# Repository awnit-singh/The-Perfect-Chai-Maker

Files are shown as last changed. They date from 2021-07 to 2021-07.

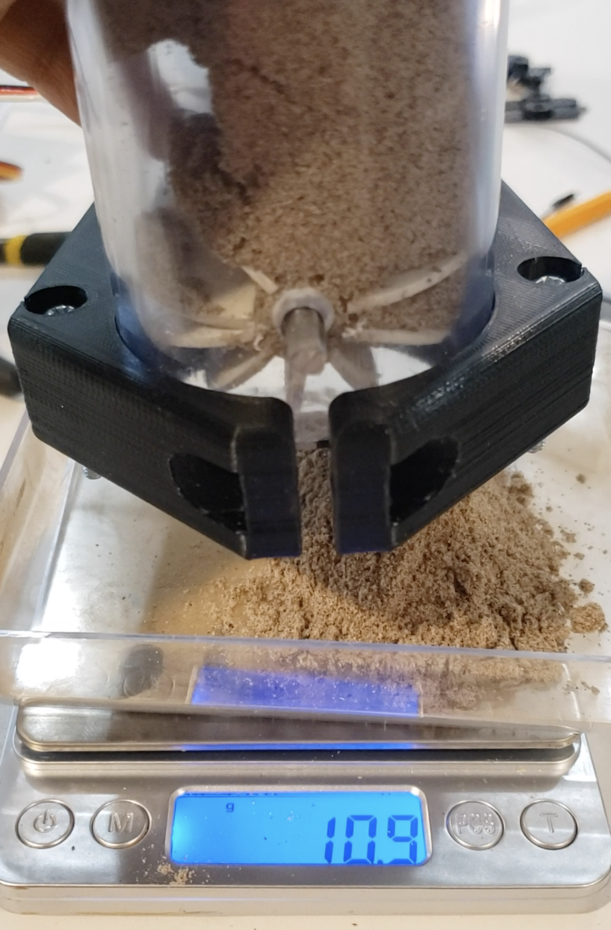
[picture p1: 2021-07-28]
Pictures/Cardamom-Measurement.png

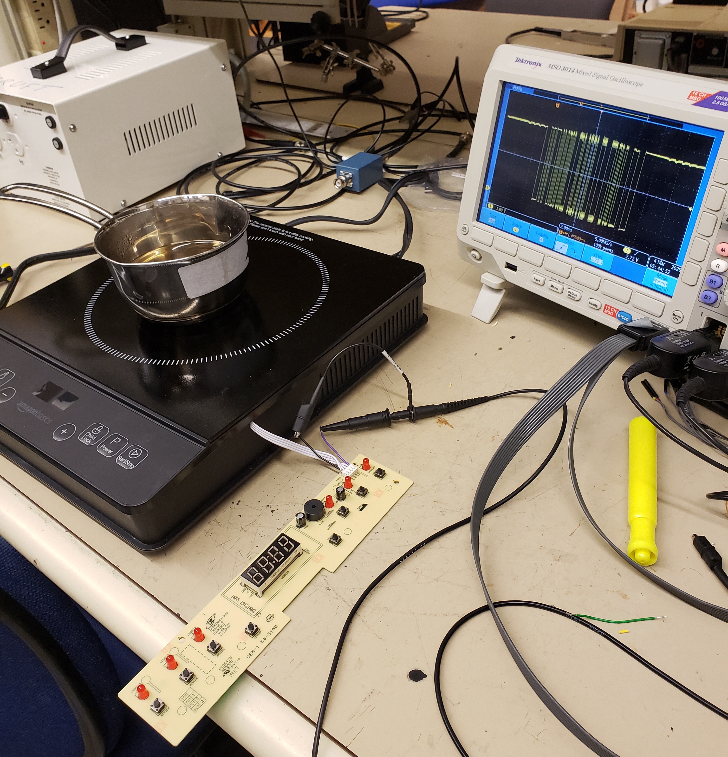
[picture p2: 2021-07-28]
Pictures/Milk-Heater-Setup.jpg

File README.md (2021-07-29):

# The-Perfect-Chai-Maker
Senior Engineering Design Project for Electrical Engineering (Honors).
https://dash.harvard.edu/handle/1/37366965

This senior thesis project presents The Perfect Chai Maker, a machine capable of making masala chai, a South Asian tea beverage, automatically. Chai is a method of making tea rather an a flavour itself. With an increasing demand for chai in the American and European market, prod- ucts have failed to replicate the traditional recipe or to improve on the inconvenience currently associated with making chai – such as time taken for preparation of the ingredients and super- vising the recipe when on the heat. This machine follows strict tolerances based on a modified version of a chai recipe to replicate a traditional cup of chai. The milk is inserted to the machine by the user though it self dispenses ingredients and hot water, taking a total of less than 5 min- utes to operate. Most of the specifications were met for the machine.
Please note that the concluding three weeks of this project were cut short due to com- plications related to the COVID-19 pandemic.

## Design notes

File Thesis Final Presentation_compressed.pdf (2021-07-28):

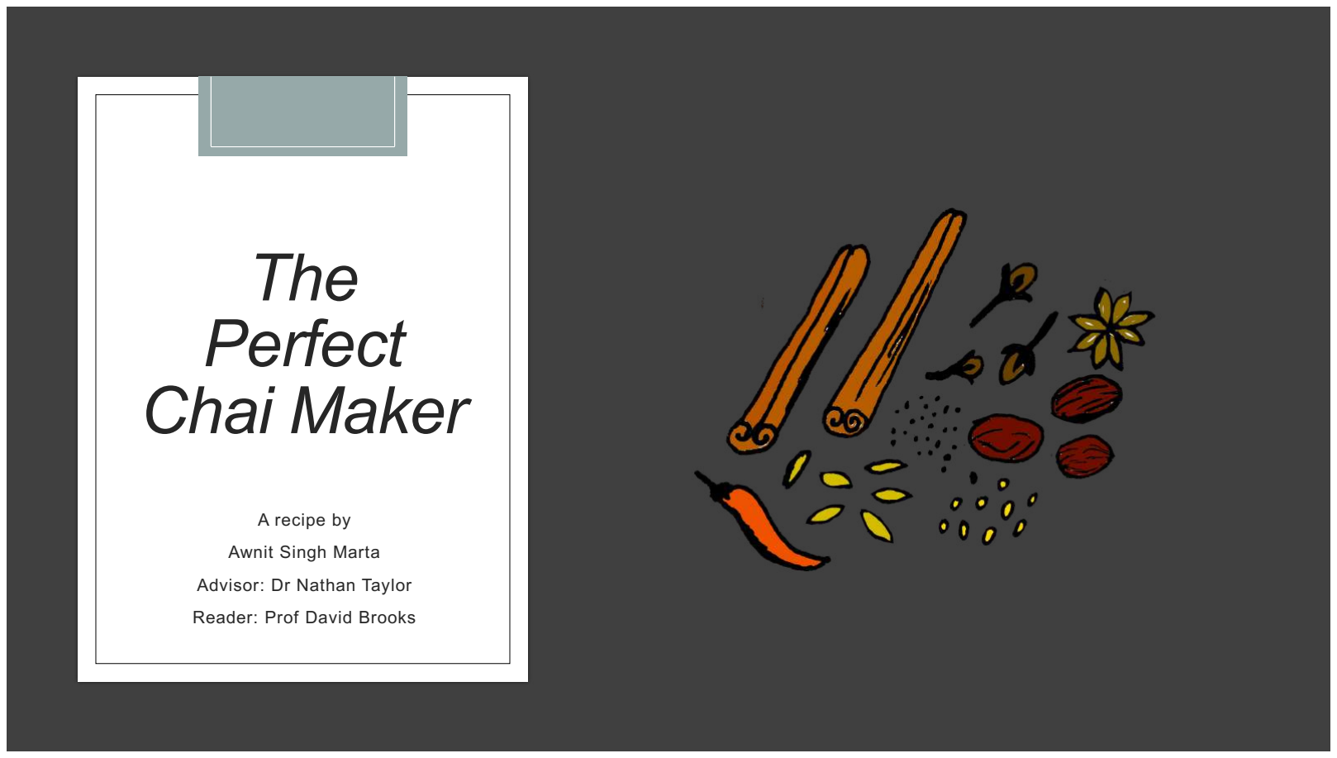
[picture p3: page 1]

# The Perfect Chai Maker

A recipe by
Awnit Singh Marta
Advisor: Dr Nathan Taylor
Reader: Prof David Brooks

# Problem

Institute for Scientific Information on Coffee, “The good things in life: coffee in the workplace,” Worcestershire, 2017.

Chai: a flavour NOT a process No dedicated chai machine in market

2 billion tea drinkers ↑+ in American market (Starbucks, Peet’s, 7/11)

67% drink ‘hot beverages’ at workplace: taste, socialize, pause & rest

Define | Design | Build | Measure | 2

# Problem

Institute for Scientific Information on Coffee, “The good things in life: coffee in the workplace,” Worcestershire, 2017.

Chai: a flavour NOT a process No dedicated chai machine in market

2 billion tea drinkers ↑+ in American market (Starbucks, Peet’s, 7/11)

67% drink ‘hot beverages’ at workplace: taste, socialize, pause & rest

Making coffee at the workplace has become an integrated part of workflow, generally requiring just the TOUCH OF A BUTTON to make. However, making Chai, a South Asian tea, has required more TIME, HANDLING of multiple components, and SUPERVISION through the process.

Define | Design | Build | Measure | 3

# Background/Existing Work

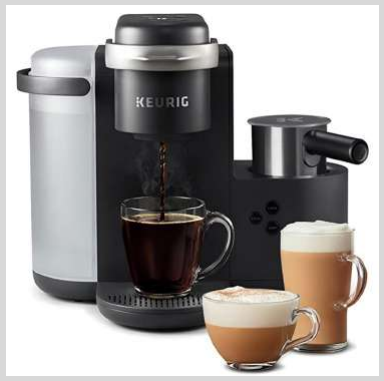
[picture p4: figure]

$199 | $220 | $250 | $450
Define | Design | Build | Measure | 4

Teas
- Insert everything
manually
- Strainer
- Induction
heater

Hot beverages
- Pod ingredients
- Reservoir for water
- Milk separately inserted
- Induction heater +
heating element

Chai
- Pod ingredients integrated
- Reservoir for water
- Milk integrated with chai
- Induction heater +
heating element

Espresso
- Pod ingredients
- Fully automated to glass
- Reservoir for water, milk
- Milk steamer + heating
element

PRODUCE | TRADITIONAL RECIPE

Chai in under 5 minutes

# Goal

Making coffee at the workplace has become an integrated part of workflow, generally requiring just the touch of a button to make. However, making Chai, a South Asian tea, has required more time, handling of multiple components, and supervision through the process.

Heat water
to 93°C
(3 min)

Insert: tea,
spices,
sugar

Simmer
(2 min)

Add milk,
bring to
boil
(3 min)

Simmer
(2 min)

Strain and
enjoy Chai!
Integrated ingredients

Minimal user involvement

S. Fountaine, “authentic masala chai recipe!,” feasting at home, 2 January 2019. [Online]. Available: https://www.feastingathome.com/authentic-masala-chai-recipe/. [Accessed 30 September 2019].
J. Pallian, “Authentic Homemade Indian Chai,” foodess, 29 November 2016. [Online]. Available: https://foodess.com/authentic-indian-chai-tea-recipe/. [Accessed 30 September 2019].
Define | Design | Build | Measure | 5

# Technical Specifications

Define | Design | Build | Measure | 6
Water temperature Milk temperature | 96 °C 85 °C | + 1 °C, − 4 °C + 5 °C, − 0 °C
Water pumped | 180 mL | ± 15 mL
Tea Cardamom and fennel seeds Sugar | 2.0 1.0 8.0 | ± 0.4 g ± 0.2 g ± 2.0 g
Time taken | < 5 mins
Size | 50 cm x 50 cm x 50 cm

PRODUCE | TRADITIONAL RECIPE

Chai in under 5 minutes

# Goal

Making coffee at the workplace has become an integrated part of workflow, generally requiring just the touch of a button to make. However, making Chai, a South Asian tea, has required more time, handling of multiple components, and supervision through the process.

Heat water
to 93°C
(3 min)

Insert: tea,
spices,
sugar

Simmer
(2 min)

Add milk,
bring to
boil
(3 min)

Simmer
(2 min)

Strain and
enjoy Chai!
Integrated ingredients

Minimal user involvement

S. Fountaine, “authentic masala chai recipe!,” feasting at home, 2 January 2019. [Online]. Available: https://www.feastingathome.com/authentic-masala-chai-recipe/. [Accessed 30 September 2019].
J. Pallian, “Authentic Homemade Indian Chai,” foodess, 29 November 2016. [Online]. Available: https://foodess.com/authentic-indian-chai-tea-recipe/. [Accessed 30 September 2019].
Define | Design | Build | Measure | 7

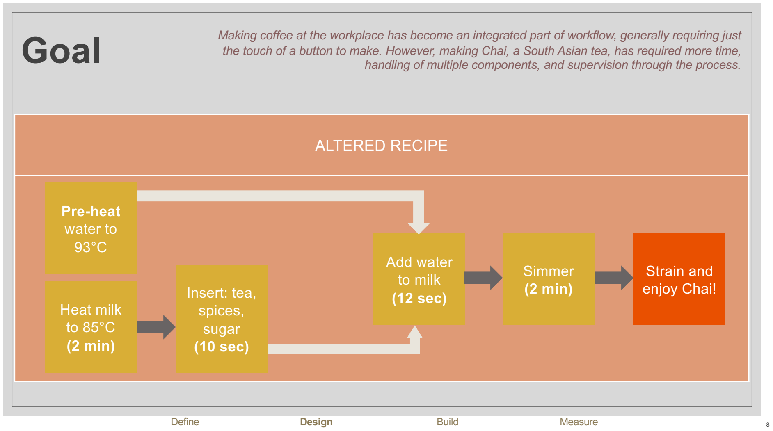
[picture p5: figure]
ALTERED RECIPE; Goal; Pre-heat water to 93°C; Heat milk to 85°C (2 min); Simmer (2 min); Strain and enjoy Chai!; Add water to milk (12 sec) Insert: tea, spices, sugar (10 sec); Define; Design; Build; Measure

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

# System Overview

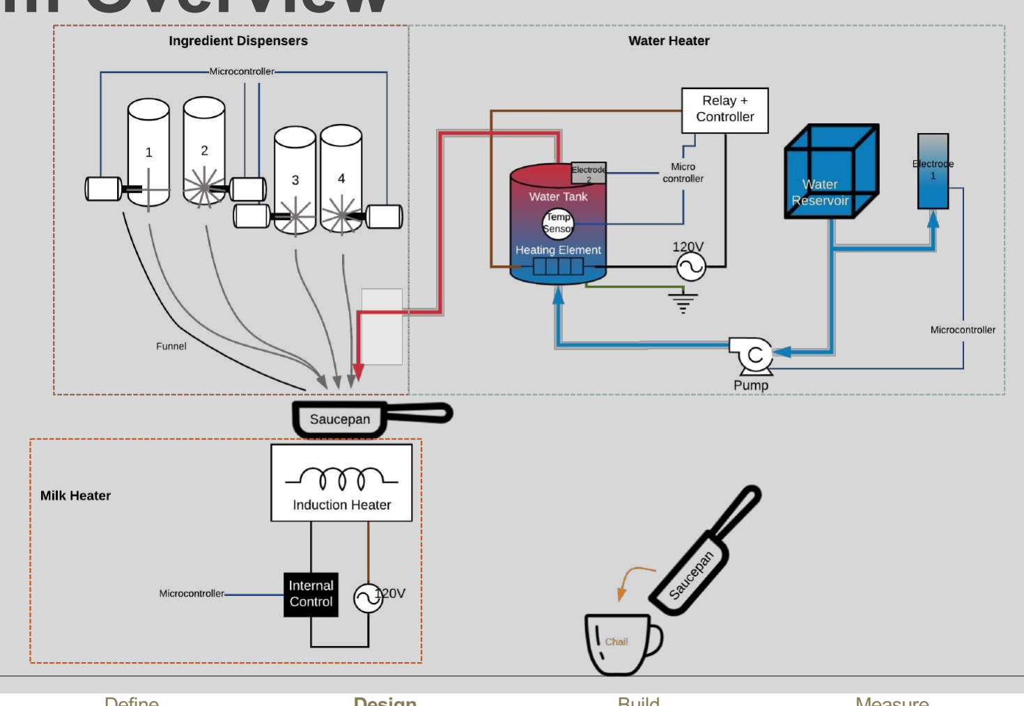
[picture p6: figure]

Define | Design | Build | Measure | 9

# System Overview

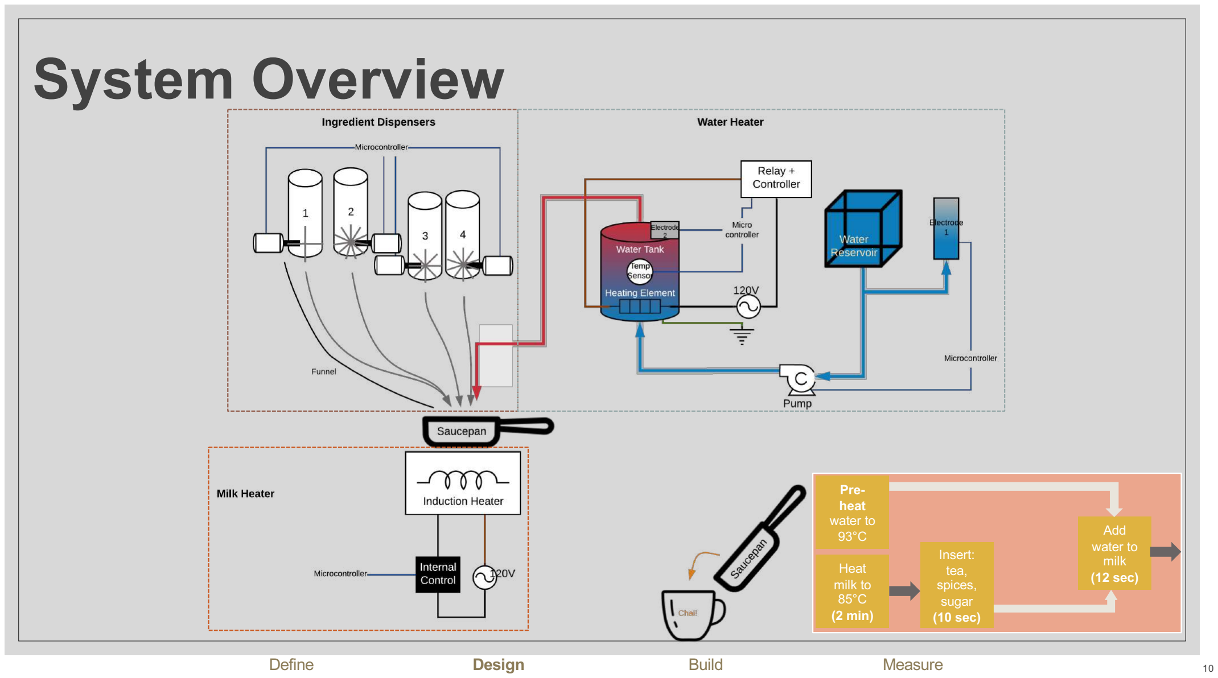
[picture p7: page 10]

Define | Design | Build | Measure | 10

Pre-heat
water to
93°C

Heat
milk to
85°C
(2 min)

Add
water to
milk
(12 sec)

Insert:
tea,
spices,
sugar
(10 sec)

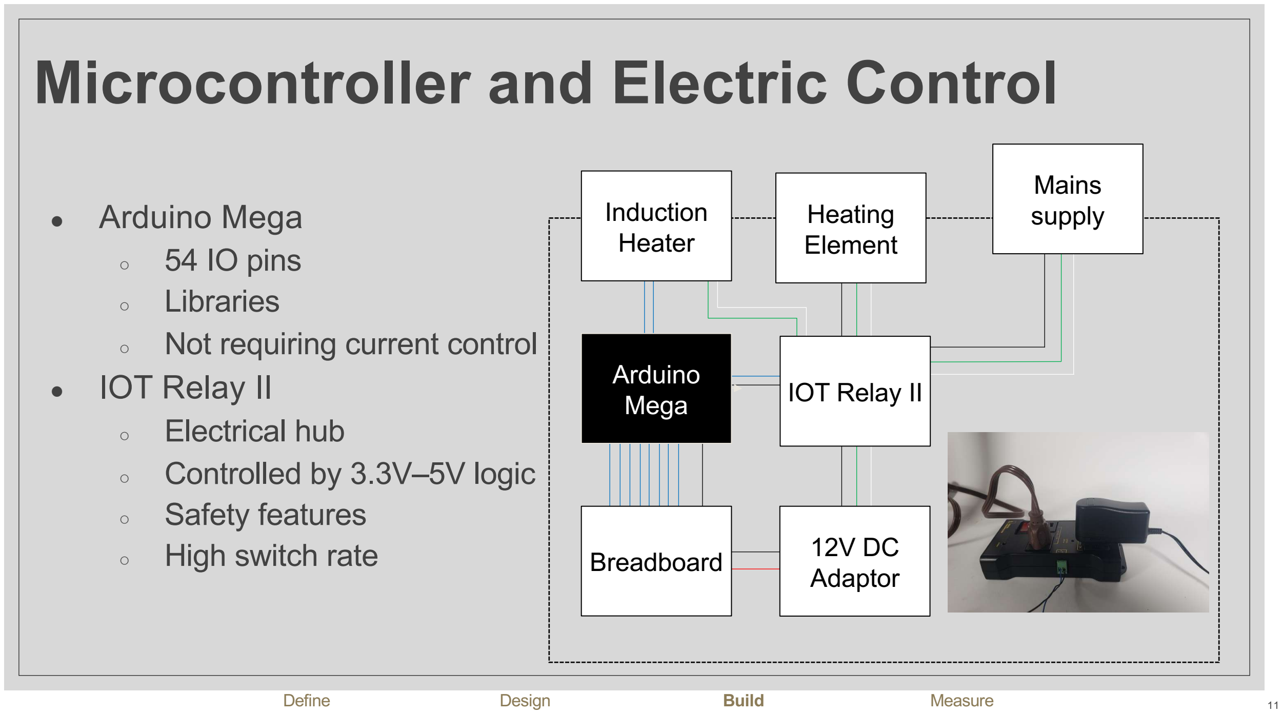
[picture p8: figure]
Microcontroller and Electric Control; ● Arduino Mega ○ 54 IO pins ○ Libraries ○ Not requiring current control ● IOT Relay II ○ Electrical hub ○ Controlled by 3.3V–5V logic ○ Safety features ○ High switch rate; Arduino Mega; Breadboard; Induction Heater; Mains supply; IOT Relay II; Heating Element; Define; Design; Build; Measure; 12V DC Adaptor

# Water Heater and Controller

12

- Water tank
- Sealed container – repurposed Keurig
- Internally secured temperature sensor

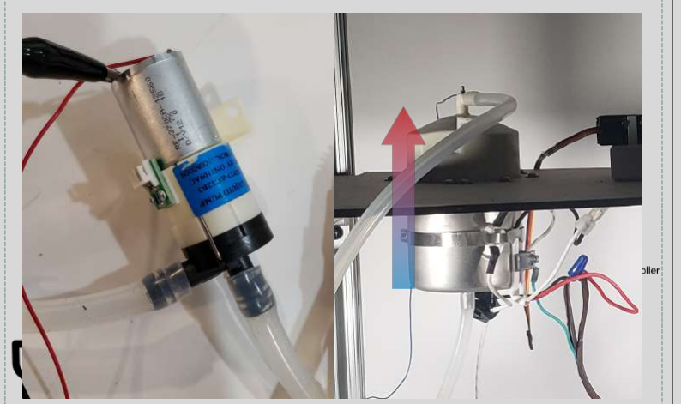
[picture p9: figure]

- Cold water enters through bottom (from reservoir), hot water leaves from top
- Keurig Water Pump
- Water flow rate within specified time
Define | Design | Build | Measure

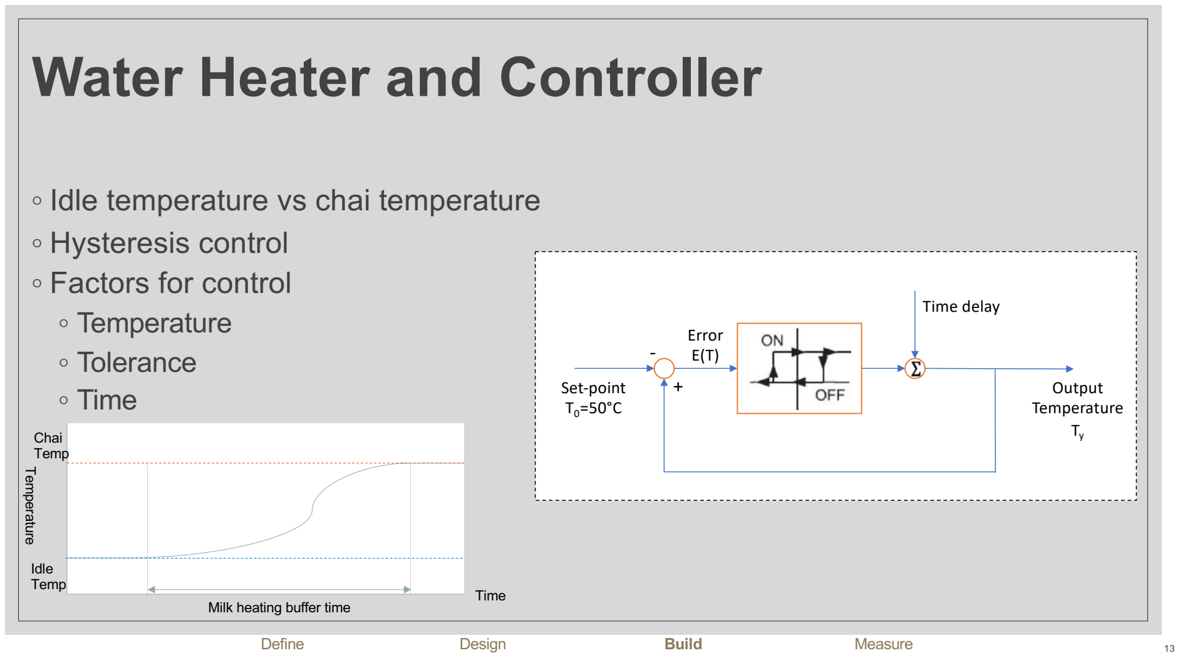
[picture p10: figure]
Water Heater and Controller; ◦ Idle temperature vs chai temperature ◦ Hysteresis control ◦ Factors for control ◦ Temperature ◦ Tolerance ◦ Time; Temperature Sensor; Water reservoir; Set-point T0=50°C; Error E(T); Time delay; Output Temperature Ty; Define; Design; Build; Measure; Idle Temp; Chai Temp Temperature; Time; Milk heating buffer time

# Ingredient Dispenser

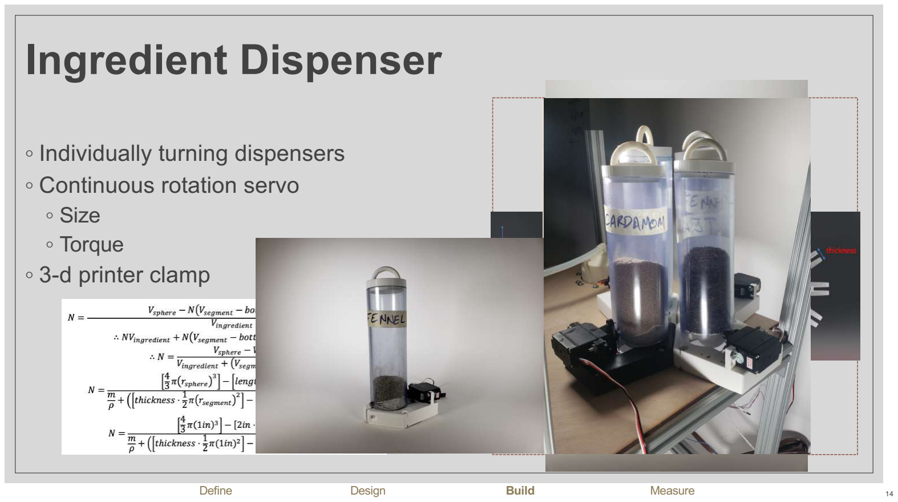
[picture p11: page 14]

14

- Individually turning dispensers
- Continuous rotation servo
- Size
- Torque
- 3-d printer clamp
Define | Design | Build | Measure

15

# Milk Heater

- Heating element vs induction heater
- Commercial conduction heater
- Tap into controls
- Safety
- Size

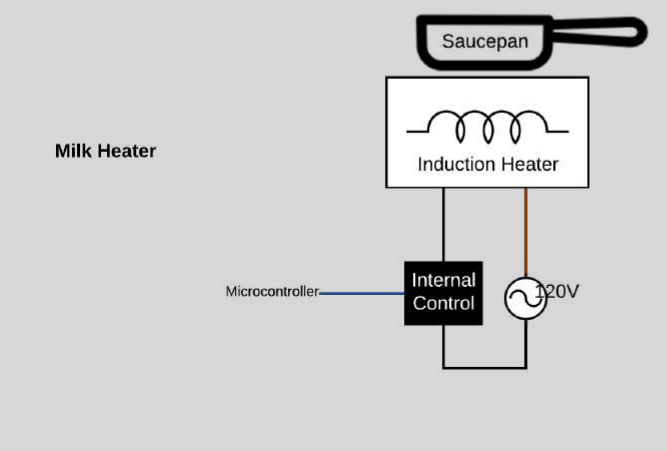
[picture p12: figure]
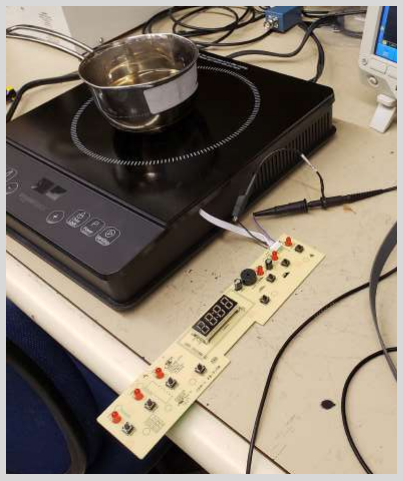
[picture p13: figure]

Define | Design | Build | Measure

# Milk Heater

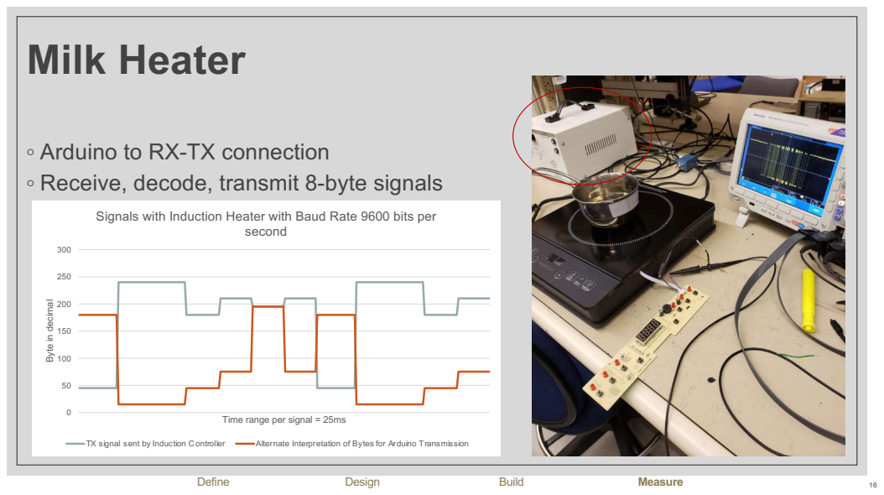
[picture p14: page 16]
second; TX signal sent by Induction Controller; Alternate Interpretation of Bytes for Arduino Transmission; Define; Design; Build; Measure

◦ Arduino to RX-TX connection
◦ Receive, decode, transmit 8-byte signals

Signals with Induction Heater with Baud Rate 9600 bits per

Byte in decimal

Time range per signal = 25ms

# Water Heater and Controller

17

- Time based
- Flowrate, rroom = 11.8 mLs⁻¹
- Flowrate, rchai = 15.0 mLs⁻¹
- Wider spread of volume but within tolerance

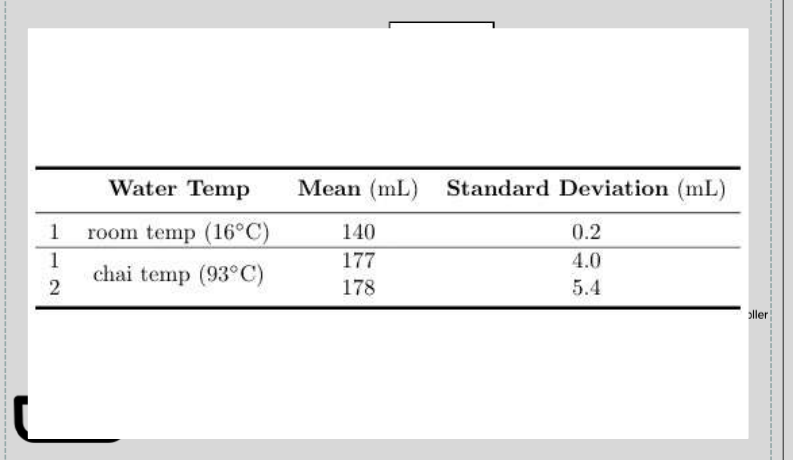
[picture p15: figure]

Define | Design | Build | Measure

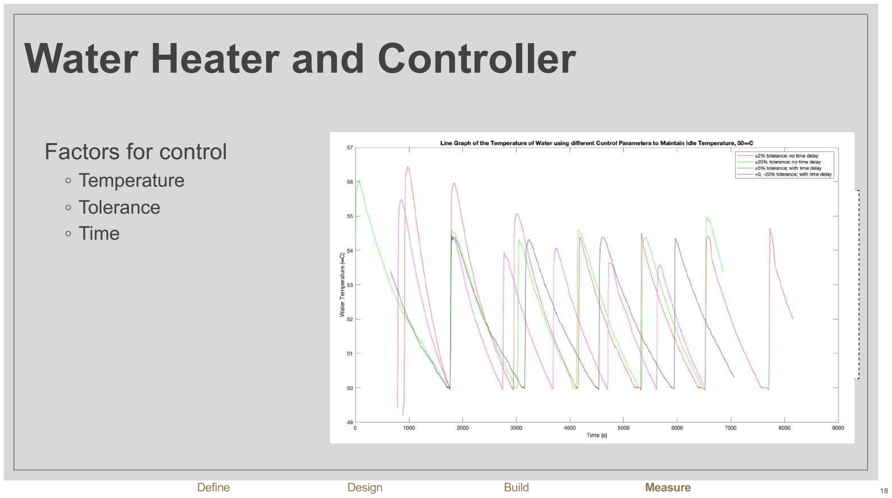
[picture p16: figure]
Water Heater and Controller; Factors for control ◦ Temperature ◦ Tolerance ◦ Time; Temperature Sensor; Water reservoir; Set-point T0=50°C; Error E(T); Time delay; Output Temperature Ty; Define; Design; Build; Measure

# Water Heater and Controller

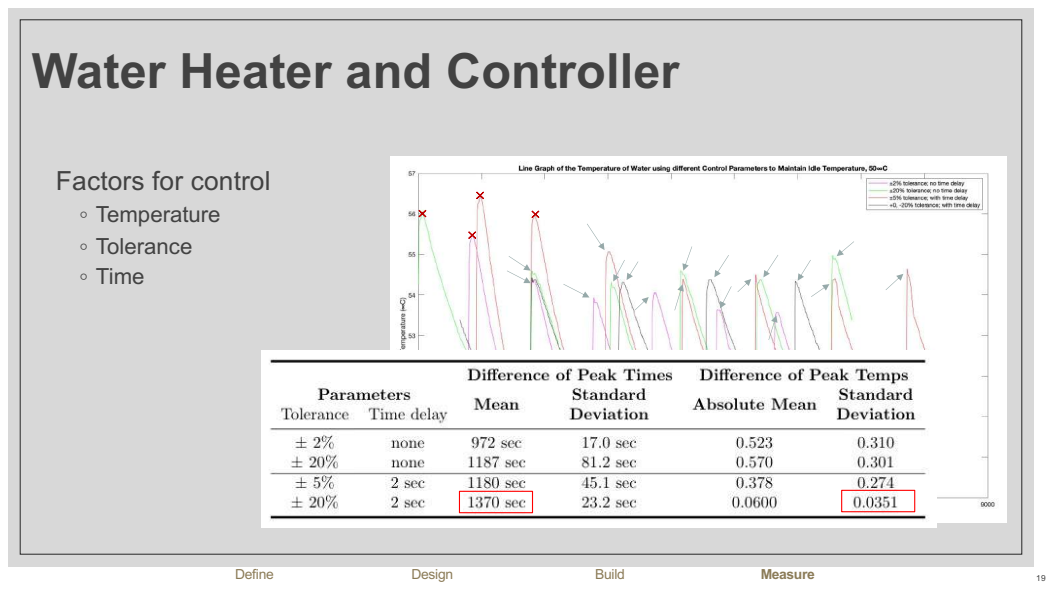
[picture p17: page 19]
Define; Design; Build; Measure

Factors for control
◦ Temperature
◦ Tolerance
◦ Time

# Ingredient Dispenser

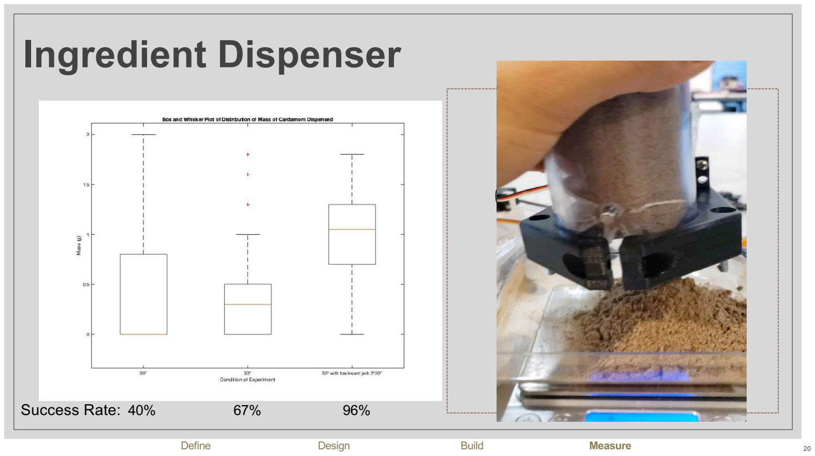
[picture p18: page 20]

20

Define | Design | Build | Measure
Success Rate: 40% | 67% | 96%

# Final Prototype

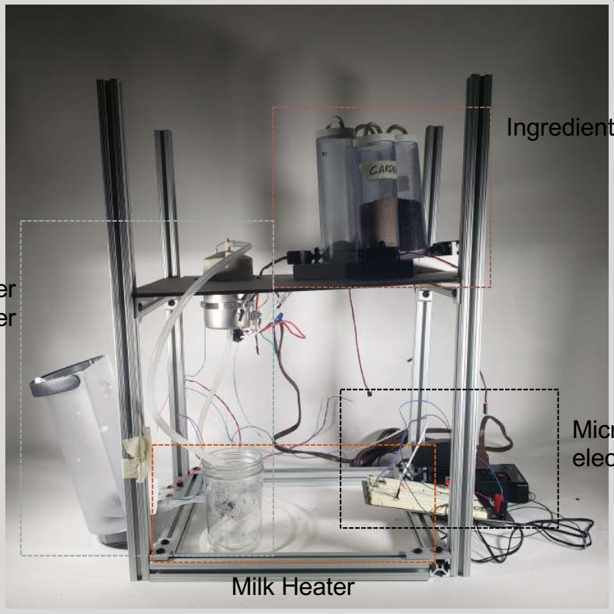
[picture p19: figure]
Milk Heater

Water
Heater

Microcontroller and
electric control

Ingredient Dispenser

21

Water temp Milk temp | 96 + 1°C, − 4°C 80 + 5°C, − 0°C | Yes Yes but not integrated
Water pumped | 180 ml ± 15 ml | Yes
Tea Cardamom and fennel seeds Sugar | 2.0 ± 0.4 g 1.0 ± 0.2 g 8.0 ± 2.0 g | Yes but tolerances not met
Time taken | < 5 mins | No
Size | 50 cm x 50 cm x 50 cm | Yes

# Conclusions

22

# Future Plans

23

Integration

Testing
Time entire process
Milk heater using immersed sensor Stable surface for ingredient dispensers Idle power usage for water heater

Tubing fitted with pressure valves PID water controller
Mixed spice dispenser

# did it make chai?

24

# thank you

25

## Nishant Nathan Evan Jim and Ben Salma ES Funhundred and the entire ES100 staff

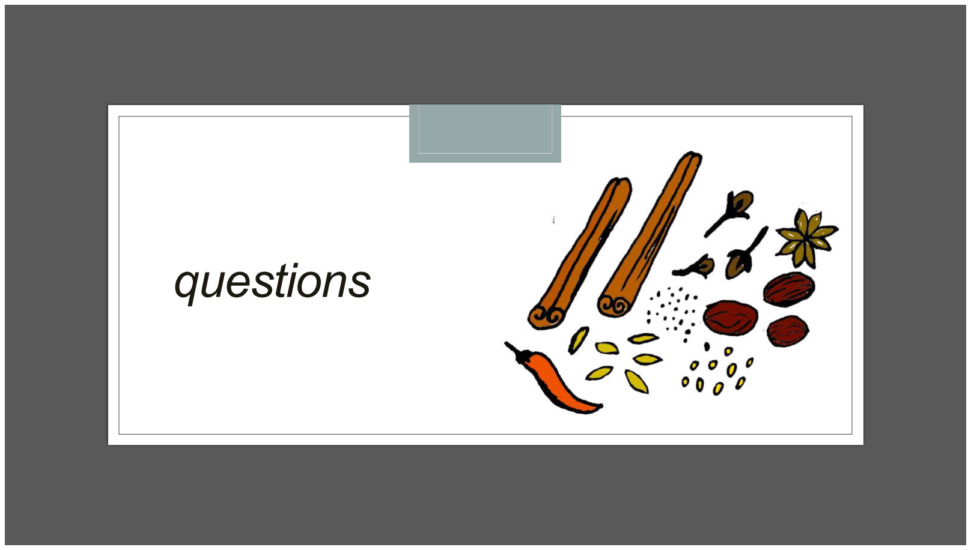
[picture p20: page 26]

# questions

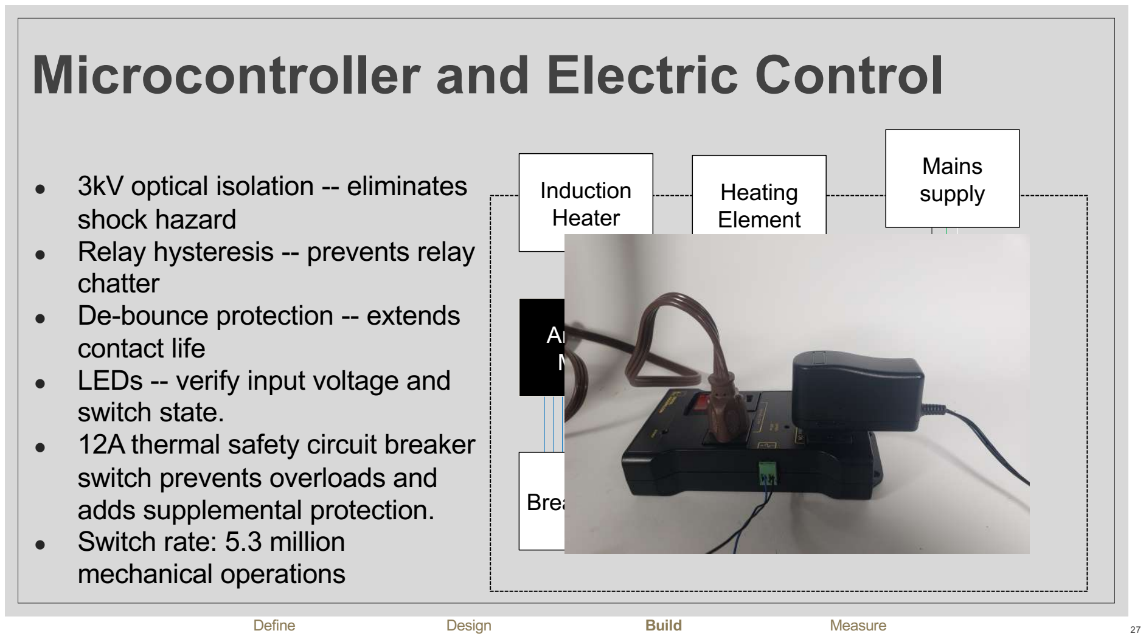
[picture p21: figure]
Microcontroller and Electric Control; ● 3kV optical isolation -- eliminates shock hazard ● Relay hysteresis -- prevents relay chatter ● De-bounce protection -- extends contact life ● LEDs -- verify input voltage and switch state. ● 12A thermal safety circuit breaker switch prevents overloads and adds supplemental protection. ● Switch rate: 5.3 million mechanical operations; Arduino Mega; Breadboard; Induction Heater; Mains supply; IOT Relay II; Heating Element; Define; Design; Build; Measure; 12V DC Adaptor

# Water Heater and Controller

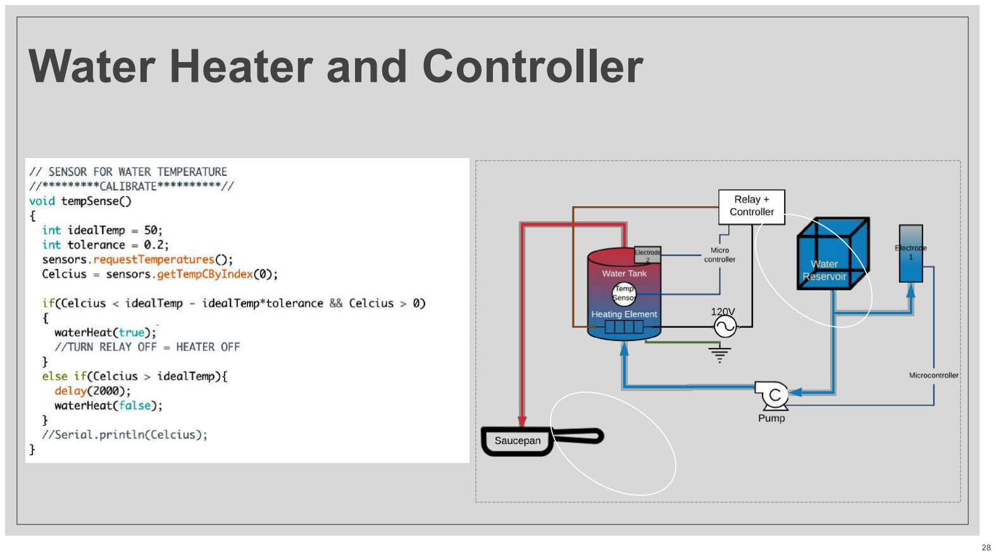
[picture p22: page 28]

28

- Verification of Presence of Water
- Electrodes in reservoir – active high
- Electrode on water tank – active low

# Water Heater and Controller

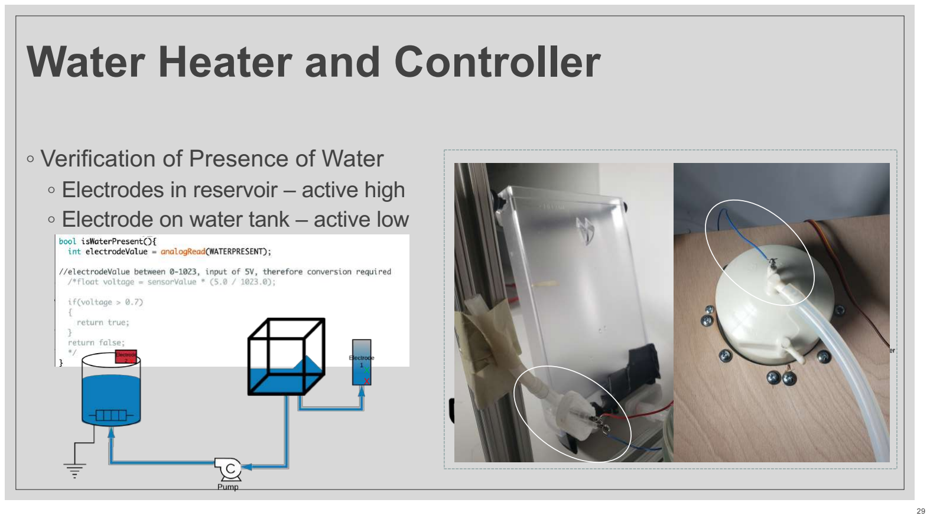
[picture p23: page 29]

29

- Verification of Presence of Water
- Electrodes in reservoir – active high
- Electrode on water tank – active low

X
X

X

Design Choices ◦ Milk inside machine? ◦ Refrigeration ◦ Clogging/cleaning of tubes ◦ Separate brewing chambers ◦ Spice choices ◦ No pods ◦ Cinnamon, ginger not used ◦ Not all required ◦ Wet vs dry ingredients ◦ Density of ingredients

30

# Water Heater and Controller

- Heating water to chai temperature
- Time = 200 sec

31

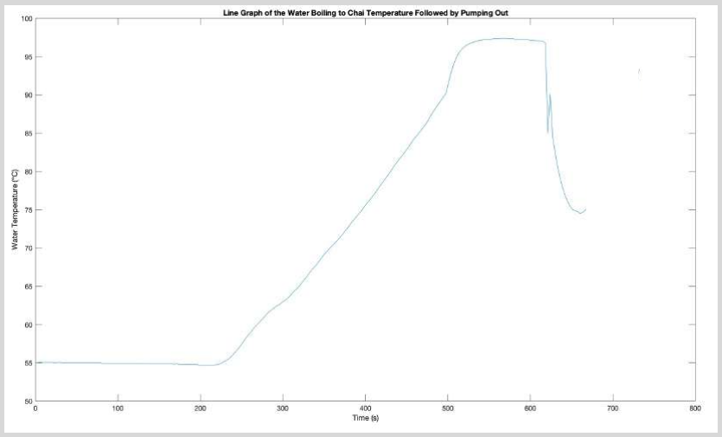
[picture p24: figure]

# Milk Heater

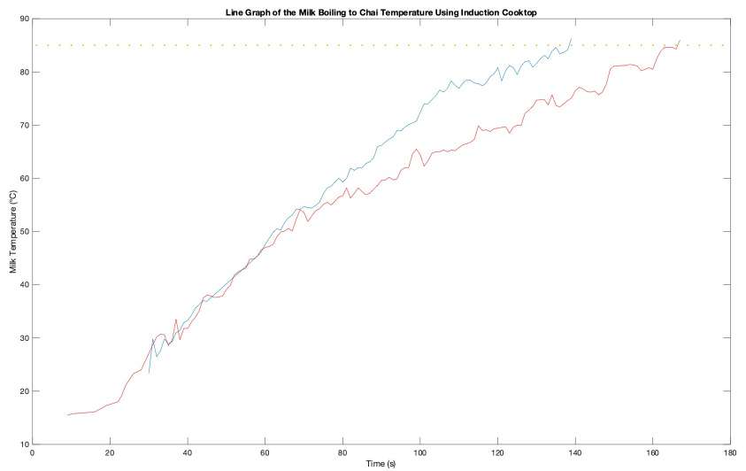
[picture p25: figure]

- Heating milk to chai temperature
- Time = 110 sec – 180 sec
- Conducted using IR sensor

32

# Ingredient Dispenser

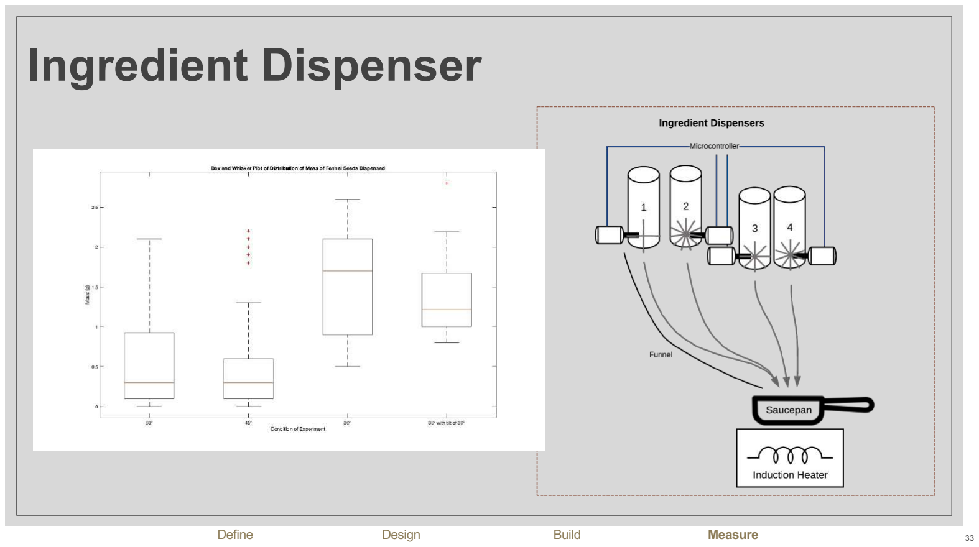
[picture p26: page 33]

33

Define | Design | Build | Measure

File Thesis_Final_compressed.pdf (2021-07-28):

# THE PERFECT CHAI MAKER

# AWNIT SINGH MARTA

Supervising Advisor: Dr Nathan Taylor Faculty Advisor: Professor David Brooks

A Senior Design Project submitted in partial fulfillment of the requirement for the degree of
Bachelor of Science in Electrical Engineering

John A. Paulson School of Engineering and Applied Sciences Harvard University

Cambridge, Massachusetts

April 10, 2020

## Contents

1 Introduction | 1
2 Problem Definition | 6
3 Design Approach | 10
4 Hardware Design | 12

i

5 Final Prototype and Conclusions | 43
6 Future Development | 45
7 Acknowledgements | 48
Appendices | 49
A Bill of Materials | 49
B Schematic | 50
C Arduino Code | 51
D Data Collection | 57

ii

D.1 Ingredient Tolerance Test | | 57
D.2 Calculating Ingredient Density | | 57
D.3 Dispensing Ingredients | | 58
D.4 Induction Heater Signals | | 61
E Data Sheets | 66

## List of Figures

1 | Study on drinking hot beverages | | 1
2 | CRAFTEA Machine | | 2
3 | Keurig K-Caf´e | | 3
4 | BrewChime Machine | | 4
5 | Nespresso Latisima Pro Machine | | 5
6 | Chai recipe | | 6
7 | Modified chai recipe | | 7
8 | Modified chai recipe flowchart | | 10
9 | System diagram | | 11
10 | Breadboard | | 12
11 | Voltage divider | | 13
12 | Relay switches | | 14
13 | Water pump mechanism | | 15
14 | Hysteresis control diagram | | 15
15 | Temperature sensor and heating element | | 16
16 | Safety features of water tank | | 17
17 | Initial control output | | 18
18 | Updated hysteresis control diagram | | 18

iii

19 | Updated control output | | 19
20 | Raising water temperature to chai temperature | | 21
21 | Controlling pump using Arduino | | 22
22 | Water electrodes | | 23
23 | Water electrode illustration | | 24
24 | Reservoir electrode schematic and Arduino output | | 25
25 | Tank electrode schematic | | 26
26 | CAD drawings of original dispenser design | | 27
27 | Dispenser design changes | | 28
28 | Final dispenser model | | 29
29 | Cardamom mass tests | | 31
30 | Cardamom mass distribution | | 32
31 | Fennel seeds mass tests | | 33
32 | Fennel seeds mass distribution | | 34
33 | Fennel seeds modified clamp design | | 35
34 | Tea leaves mass tests | | 36
35 | Flaws of tea leaves dispenser design | | 37
36 | Dispenser attachment | | 37
37 | Milk heat test | | 39
38 | Induction heater testing | | 40
39 | Induction heater signal transmission | | 41
40 | Final prototype | | 43
41 | Auger lift dispenser design | | 46
42 | Milk stored in machine design | | 46
43 | Final schematic | | 50

iv

## List of Tables

1 | Technical specifications | | 9
2 | Control parameter comparisons | | 20
3 | Effect of temperature on flow rate | | 22
4 | Dispenser final design | | 28
5 | Technical specification analyses | | 44
6 | Measuring mass to determine tolerance | | 57
7 | Fennel seed mass tests | | 59
8 | Cardamom mass tests | | 60
9 | Tea leaves mass tests | | 61
10 | Off state signal transmission | | 62
11 | Standby state signal transmission | | 63
12 | Induction heater on state signal transmission | | 63
13 | Induction heater intermediate on state signal transmission | | 64
14 | Induction heater off state signal transmission | | 65

v

# Abstract

This senior thesis project presents The Perfect Chai Maker, a machine capable of making masala chai, a South Asian tea beverage, automatically. Chai is a method of making tea rather an a flavour itself. With an increasing demand for chai in the American and European market, products have failed to replicate the traditional recipe or to improve on the inconvenience currently associated with making chai – such as time taken for preparation of the ingredients and supervising the recipe when on the heat. This machine follows strict tolerances based on a modified version of a chai recipe to replicate a traditional cup of chai. The milk is inserted to the machine by the user though it self dispenses ingredients and hot water, taking a total of less than 5 minutes to operate. Most of the specifications were met for the machine.

It shall be noted that the concluding three weeks of this project were cut short due to complications related to the COVID-19 pandemic.

vi

## 1 Introduction

### 1.1 Motivation

There are over 2 billion daily tea drinkers around the world; approximately 165 million cups are drunk daily in the UK, averaging to three cups per person. The Chai Latte has become an increasingly popular drink since its introduction around 2 decades ago; however, this mixture of concentrated “chai” syrup and milk is not a true form of chai. Making masala chai, a traditional South Asian tea beverage, is a lengthy process. Contrary to popular belief, chai is not a flavour, rather, it is a process of making tea with a range of spices and milk. This requires more time, both for preparation and clean up, as well as accounting for different needs for each person, for example spice or sugar ratio, or the type of preferred milk. At the typical workplace, coffee machines are a common sight allowing one to make coffee in a couple minutes; however, making a cup of English breakfast tea – the closest alternative to chai – requires much more time and effort. The customary aspect of chai closely aligns to reasons that employees at a workplace may want to drink it. In a study conducted by the Institute for Scientific Information on Coffee, as shown in Figure 1, three of the most prominent categories for drinking coffee at work were to: socialise with colleagues, feel less tired, and get some time to pause and rest, all of which are important concepts with the social tradition revolving chai.[1]


Figure 1: Percentage of people who responded to study on reasons for drinking hot beverages at work.[1] The customary aspect of drinking chai closely aligns to the top three selected options.

This project aims to bring together electrical engineering concepts with novel commercial product development. By using knowledge derived from control systems and analogue/digital circuitry design, this thesis will produce an optimised solution to the posed problem. The goal of the project is to produce a prototype machine that brings an authentic cup of chai to homes and offices at the touch of a button – a discussion of what is meant by ’authentic’ is provided in Section 2.1. With its low maintenance and low user-involvement design, it would be a convenient, time efficient, and mess free solution to the traditional method of chai making.

### 1.2 Problem Statement

Making coffee at the workplace has become an integrated part of workflow, generally requiring just the touch of a button. However, making chai, a South Asian tea, or the closest alternative, has required more time, preparation, and handling of multiple components.

### 1.3 Background Research and Existing Work

There are many machines that make hot beverages and ”chai flavoured” drinks. The four products, however, that were focused on allow a spectrum of approaches to making both coffee and tea be taken into account: CRAFTEA, Keurig K-Caf´e, BrewChime, and Nespresso Latisima Pro. These products have varying levels of automation and involvement from the user to produce a beverage.

CRAFTEA is an induction heating kettle that requires all ingredients to be inserted by the user and a control screen allows a time to be set for making the tea. CRAFTEA does not come with a scoop or other measuring system for the ingredients, so one would have to manually measure those – adding to the preparation time; however, lines on the inside of the pot do indicate how much water or milk has been added. The main advantages of this machine are its form factor, strainer (see Figure 2) and custom brewing features. This allows users to not have to worry about having spare tea leaves or spices in the serving mug, as well as ensuring that only one thing – the kettle – needs to be cleaned. The cost of this machine is $199.[2]

(a) (b)

Figure 2: Front (a) and top (b) view of the CRAFTEA machine. This machine does not have an automation focus for making chai or other tea drinks.

Keurig K-Caf´e is a pod based beverage maker with a reservoir to store and preheat water and an induction heater-operated milk frother, see Figure 3(a). To make a beverage, the user inserts a K-Cup (costings upwards of $0.50), see Figure 3(b), and selects the volume of the beverage from one of four options.[3] The brewing

process happens as the water passes through the K-Cup, with a dedicated pump to add pressure, which replaces the requirement of time to brew the coffee/tea. Should the user require frothed milk, it can be inserted in the provided saucepan and a selection of three buttons allow the user to choose the heat of the milk. This would then be manually inserted to the mug that the water-based beverage is made in. For the Keurig K-Caf´e, the saucepan would be the only item needed to be cleaned by the user. The machine costs $199.99 though there is a recurrent cost of replenishing the single-use K-Cups.[4]

(a) (b)

Figure 3: Front view of the Keurig K-Caf´e machine (a) and single-use K-Cups inserted into the Keurig to make a beverage (b). [3, 4] The Keurig has two separate mechanisms to make the beverage and to froth milk.

The BrewChime machine is designed specifically for making chai, the goal of this thesis, by using two separate compartments for heating water/brewing tea, and heating milk. The main control is a jog wheel/button for selecting the drink size and tea strength. The screen instructs the user how much milk to insert into the carafe. This machine also uses pods, whereby the user inserts a pod to the top of the brewing compartment and manually inserts milk into the pot for the lower milk heating compartment. The brewed tea pours into the milk due to its position above the water before being ready for serving. The main advantage, alongside the fact that this machine is dedicated to make as close to an authentic cup of chai, is that the ingredients are integrated inside the water to brew, rather than the water passing through the pod.[7] However, some of the major disadvantages are the use of the limited number of pods, which cost just over a dollar per chai; using the limited number of flavoured pods is quite wasteful for the environment (though they are recyclable) and the machine cannot be used unless a pod, which are exclusively produced by BrewChime, is inserted into the machine; the user is quite involved in the process of making the chai as both the milk and the pod have to be manually inserted, and multiple parts of the machine (the brewing chamber and the carafe) have to be cleaned after every use – it is also recommended that a ”clean cycle” is run after every ”50-60 brews,” adding additional hassle for the user.[6, 7]


Figure 4: Front view of the BrewChime machine. In the top left is the boiling water/brewing compartment, with a strainer to not allow the ingredients to pass through, below is the carafe for milk heating and final production of chai, and the top right has the touch screen display and water reservoir (not visible in figure).

Finally, the Nespresso Latisima Pro machine automates the entire process of making hot beverages, specifically, lattes, cappuccinos, and espressos.[8] There are two removable reservoirs in the machine, as seen in Figure 5, one for milk and the other for water. The removable milk reservoir allows it to be stored in a fridge, avoiding the milk from going bad while also ensuring that the machine has complete control over how much milk is inserted. With a touch screen interface, can control the size and type of drink. The advantage of a machine like the Latisima is that the user does not need to clean anything to make a drink – after each use, the milk container pipe released steam to clean the pipe. This container, however, does need to be rinsed after many uses, depending on how often and how old the milk in the carafe is. This device is priced at $749.99, making it significantly less accessible and affordable than the other three machines combined.[8, 9]

(a) (b)

Figure 5: Front view of the Nespresso Latisima Pro machine (a) and single-use Nespresso pods inserted into the Nespresso Latisima Pro to make a beverage (b).[8] The Nespresso requires the least effort from a user to make espresso based beverages, comes with a removable milk carafe to ensure freshness but is the most expensive.

## 2 Problem Definition

### 2.1 Chai Recipe

There are many forms, recipes, and varieties of making masala chai.[10] The recipe of making chai chosen for this chai maker illustrated in Figure 9, is required to be specifically quantified in order to create technical specifications and set constrains. The following one has been chosen for its precision with the ingredients, ties to the traditional method, and its yield: one large mug. The time taken by this recipe is 10 minutes of cooking and 5 minutes for preparation.


Figure 6: Flowchart of a typical recipe of making chai. Chai requires a step-by-step process of heating, inserting ingredients, boiling, and simmering.

The ingredients for such a recipe are [11, 12]:

- 180 ml water
- 90 ml whole milk

– can be substituted with any vegan/lactose free option

- 10 grams sugar
- 2 grams black tea (1 tablespoon loose-leaf)
- Variety of spices (optional)

– 2 pinches ground cardamom
– 2 pinches fennel seeds

– 2 slices fresh ginger

– 1 cinnamon stick

The recipe is:

1. Heat water to 93◦C

2. Insert sugar, spices, tea and bring to boil
3. Add milk and bring to boil
4. Lower the heat and simmer for 5 minutes
5. Strain into a glass

### 2.1.1 Adjustments and Additions to the Recipe

First of all, as fresh ginger is required in this recipe, the machine dod not include this spice. This is as the ginger would need to be (1) cut into pieces, which cannot be guaranteed to be standard and (2) if fresh ginger is kept cut in dispensers, it would eventually dry out. Cinnamon sticks were also not be used in this recipe as their freshness in powdered form would not equate a stick and cracked cinnamon sticks do not have a consistent granularity.

Secondly, 2 pinches of cardamom and fennel seeds are approximately 1 gram.

Finally, the milk and water will be heated separately before being added together, reducing the time taken to heat and boil the liquids, both in step 1 and 3 shown in Figure 9. According to the Royal Society of Chemistry, 65◦C is the optimal temperature to drink tea [13], therefore the final product will be served

to this temperature.

### 2.1.2 Time for Making

For users at the workplace, reducing the time required to have a ready drink is key. The preparation time for the user is effectively 0 as the user is not required to prepare any of the ingredients. The only exception for this is when the machine is running low on ingredients or water. Furthermore, the machine should make the drink in less than 5 minutes, reducing the time taken by half. The modified recipe is illustrated in Figure 7.


Figure 7: Flowchart of the redefined chai recipe for this machine. The modified recipe ensures that a traditional cup of chai is made while reducing time through conducting simultaneous processes.

### 2.1.3 Cleaning of Machine

Cleaning the machine is the key inconvenience and non-automated process of the machine, therefore it must be reduced. The final design should only have one container that requires cleaning: both the insoluble spices and tea, and the milk residue should end up in a single container that can be removed. Due to this, the machine will not store milk, reducing the automatic nature of the machine as storing the milk would require: refrigeration, regular cleaning of tubes, all of which significantly affect the purpose of the machine.

### 2.1.4 Tolerances

As with any recipe there is leeway with the inserted ingredients, and the tolerances will determine the precision of the components. The milk is inserted manually into the machine; however, the rest of the ingredients (water, sugar, spices) are dispensed by the machine. The machine will assume the user inserted milk is correct as verifying this adds complexity beyond the necessity of the goal of the thesis. An experiment of pouring the dry ingredients using a tea spoon 10 times revealed the tolerances listed in the technical specifications, see Appendix D.1, depicting the leeway in a typical human measuring ingredients.

As the modified recipe has an idle water temperature and a heated chai temperature, the tolerances for these differ. For the idle temperature, the tolerance can be larger as the controller maintains this fluctuating temperature during the time that chai is not being made. Therefore, this tolerance is ±20%. When chai is made, the water is heated to the chai temperature, with a tighter tolerance of approximately +1%, –5%, according to temperatures taken during experimentation by making chai.

For the milk temperature, reaching close to the boiling point while avoiding spill over is important. Should the boiling point be exceeded, milk would spill on the components and cause damage. However, this temperature also cannot be too cold since the ingredients need to adequately brew. Therefore, the tolerance was set for 80◦C +5◦C, -0◦C.

### 2.1.5 Size

To accommodate office spaces, the machine must take into consideration the average counter top size. The machines discussed in Section 1.3 are sized: 28cm × 23cm × 33cm, 44cm × 36cm × 37cm, 34cm × 28cm × 28cm, and 27 × 20 × 33cm respectfully. The size of The Perfect Chai Maker therefore should not exceed 50cm × 50cm × 50cm.

### 2.2 Cost

The total cost of the machine should be less than the average cost of an office space coffee machine as well as the main competitors. Since the BrewChime is most closely aligned to this machine, the cost of the machine should not exceed $200. This machine would not have the recurring cost for pods, making it cheaper in the long term. The cost of per chai using the ingredients in this machine is $0.30, significantly lower than the

cost of pods for the analysed machines – see Appendix A for cost breakdown.

### 2.3 Technical Specifications

The prior analysis and the refined chai recipe inform the development of quantitative functional requirements, outlined in Table 1.

Specification | Target
| Value | Tolerance | Units

Process
Time to make chai | < 5 | | mins
Pump: Hot water is transferred from the wa-
ter tank to the mixing container | 180 | ±15 | mL

Controller: Maintenance of idle temperature
when machine is not in use | 50 | +5 | ◦C

Time taken to raise milk and water tempera-
ture | 120 | −0
| | +10 | secs

Ingredients
Temperature of water when making chai | 96 | −4
| | +1 | ◦C
Temperature of milk when making chai | 80 | −0
| | +5 | ◦C

Dispense:
Tea leaves | 2 | ±0.4 | g
Sugar | 8 | ±2.0 | g
Cardamom | 1 | ±0.2 | g
Fennel seeds | 1 | ±0.2 | g
Other
Device Size | 50x50x50 | | cm³

Table 1: Technical specifications for the implementation of The Perfect Chai Maker. Using the conducted analyses and the developed recipe, the specifications for the build of the machine were formed.

## 3 Design Approach

### 3.1 Modifications to Recipe

The approach to the design of the machine was implemented by adjusting the recipe to optimise the process of making chai. Firstly, to ensure that the user only needs to clean one part of the machine and because milk cannot be stored in the machine (see Section 2.1.3) means that the ingredients would have to be inserted directly into the milk rather than letting them steep in the water first. Secondly, to decrease time, two separate heating devices are designed so that the heating process can be done simultaneously, rather than consecutively. See Figure 8.

The updated recipe therefore is:

1. Heat water to 93◦C; heat milk to 85◦C
2. Insert sugar, spices, tea to milk and simmer for 2 minute
3. Add water and bring to boil
4. Lower the heat and simmer for 2 minute
5. Strain into a glass

Figure 8: Flowchart of the modified version of making chai. The user has to insert milk into a carafe where all the ingredients combine together. This process allows the time taken to make chai to be reduced and ensures that all ingredients end up in one container, reducing cleaning time. The colour of the boxes indicate the container of storage, for example orange is for the user-inserted carafe. The green lines indicate transfer of ingredients, the red lines indicate the control systems.

### 3.2 System Diagram

The overall system is divided into four subsystems:
1. Micro-controller and power: This subsystem deals with supplying power to the different subcomponents in the machine and making sure that they interact in the correct way.

2. Water heater and control: This subsystem ensures that the machine has enough water to make chai; maintains water either at a resting (idle) temperature when the machine is not in use or heats it up to the chai temperature; and pumps the appropriate amount to the carafe when needed.
3. Ingredient dispenser: This subsystem dispenses the dry ingredients, each with specific required amounts, to the carafe while ensuring that steam from the milk/water does not penetrate, thus ruin, the ingredients.
4. Milk heater: This subsystem heats up the milk within the limited time frame before simmering all the ingredients to produce the final product.


Figure 9: System diagram of the final prototype model. See Section 4 for hardware design choices.

The user can indicate making chai by pressing a button for a 3 seconds. This notifies the Arduino to start heating the milk and the water. Once the milk is sufficiently heated, the ingredients are dispensed into the milk carafe – the funnel ensure that they fall into the carafe as the dispensers do not sit directly above the carafe. Then, once the milk has reached the chai temperature, the hot water gets inserted into the milk and the concoction simmers until it is ready. The user can remove the carafe from the machine and pour it into a mug to enjoy the chai while ensuring that the ingredients get filtered by the mesh that covers the carafe.

## 4 Hardware Design

### 4.1 Micro-controller and Power

### 4.1.1 Arduino Controller

The micro-controller for this project is an Arduino Mega 2560 R3 due to its many component compatible libraries and abundance of analogue and digital pins. The micro-controller also did not need to source current. Initially, more pins were thought of as a requirement because of the use of multiple servos; however, only one pin is needed per servo and a 16-channel PWM/Servo shield is also able to solve that issue. Figure 10 shows the wired connections from the Arduino to the breadboard, which then branch to individual components, for example input to the relay switch.

### 4.2 Power Management

### 4.2.1 Voltage Divider

There are three current requirements for the machine: 120V AC for the water heater, 120V AC for the milk heater, and an AC to DC 12V–1A adapter to power the Arduino, pump, and servos. A breadboard is used to hold all the components, as shown in Figure 10.

Figure 10: Breadboard with components and connections from the Arduino to the machine. Red represents 12V, yellow is 5V, blue for control signals from the Arduino, and black is common ground. The Arduino is not in this image as it was in an inaccessible lab and the servo motors also were not attached when this photo was taken.

To power components which would require 5V, rather than 12V, a voltage divider and a unity gain buffer amplifier is used to transfer the voltage from the first circuit, having a high output impedance level, to a second circuit with a low input impedance level, see circuit diagram in Figure 11. The interposed buffer prevents the second circuit from loading the first circuit unacceptably – with a sudden increase in current use – and interfering with the desired operation of the pump, whose flow rate depends on the input current.


Figure 11: Operational Amplifier LM358 is used to allow components such as the 12V water pump to not interfere with the operation of the servos.

### 4.2.2 Relay Switch

The water heater converts AC electrical energy into heat through the process of Joule heating. Current through the element encounters resistance, resulting in heating of the element. Therefore, controlling the current input will change the amount of heat generated. This can be done either by changing the AC input to the heating element or by turning the heater on and off. The latter method can easily be done using a relay switch. The electromagnetic relay switch originally used required a significant current draw that the Arduino was not able to provide. An Arduino logic-operated BJT allowed the relay switch to be triggered by the flow of current, shown in Figure 12. One of the concerns with this set up was its lack of insulation, therefore it was replaced with an IOT Relay II, which does not require a driver and offers four outlets. This allows the IOT Relay to act as a hub for all three current source as well as provide safety for the user.

(a) (b)

Figure 12: Image of (a) original JQX relay used that was replaced by (b) IOT Relay II. The latter switch is insulated, allows multiple outlets to be plugged into one consolidated brick, and does not require the Arduino to have a separate current driver.

The relay switch, additionally, has the following benefits (see Appendix E): relay hysteresis, preventing relay chatter; LEDs to verify an input voltage and the switch state of the Arduino; a 12A thermal safety circuit breaker to prevent overloads and add supplemental protection; and a switch rate of 5.3 million mechanical operations, providing a long operational life.

### 4.3 Water Heater and Control

### 4.3.1 Water Heater

The water heater was reconfigured from a used Keurig machine. The sealed water tank is bolt-fastened, contains a heating element, has a volume of 800mL, and has holes for tubing on the top and bottom, making it ideal for the machine. A pump connects a water reservoir to the bottom hole of the tank only - as illustrated in Figure 13, because hot water rises, there is no necessity for a secondary pump to transfer the water out since pumping cold water in from the bottom would lead to the hot water leaving from the top hole.


Figure 13: Illustration of hot water transfer by pumping cold water from the reservoir. The cold water inserted by the pump pushes the hot water upwards and into the tube that goes out to the carafe. The pump and water tank are reconfigured from a used Keurig machine.

When chai is not being made, the water temperature is maintained at 50◦C, as written in Section 2.3.

The controller used to heat the water up is hysteresis or ’bang-bang’ control, whereby the heating element is controlled only by turning it on or off, shown in the control diagram in Figure 14.


Figure 14: Control diagram for water temperature. The error, E(T), which is the difference between the temperature measured by the sensor (output temperature) and the set point temperature, is used to determine whether to turn the controller on or off.

The controller receives temperature feedback through a digital thermometer, DS18B20, which has been sealed inside the water tank using a food-safe, water and heat withstanding adhesive, and mechanically secured outside of the tank, as shown in Figure 15. The adhesive also has a yield tensile strength of 3000

PSI. The sensor is placed in the middle of the tank and protrudes as close to the centre of the tank to ensure an accurate average temperature of the water is taken.

Figure 15: Image of temperature sensor being glued into the water tank. The adhesive is food-safe, can withstand temperatures above 100◦ and has mechanical strength.

### 4.3.2 Safety Features of Water Tank

Though the controller expects the water temperature to never exceed 100◦C, the circuit has been modified to

include a thermoswitch, thermal fuse, and the tank itself is connected to earth ground. The thermal switch is an electromechanical device which opens and closes contacts to control the flow of current in response to temperature change, with a threshold for 105◦C whereas the thermal fuse would physically break the circuit.

Finally, the earth ground helps carry unexpected electrical charges from other sources away safely, especially since the current intake to the circuit can exceed 10A. These components are attached using a Jubilee clip along the circumference of the tank, shown in Figure 16. The tank is securely bolted to the laser cut wooden frame board of the machine.


Figure 16: Image of thermal switch secured to tank with a Jubilee clip. The thermal switch, thermal fuse, and ground cable ensure that the user is kept safe in the case of excessive current or heat transfer. The tank is bolted to the machine’s laser cut wooden frame board.

### 4.3.3 Controller

The controller focused on two parameters: temperature tolerance and time. Initially, with a tolerance of ±2% (pink in Figure 17), the issue was that a tight tolerance of 2% cannot be obtained due to the overshoot caused by the remnant heat of the heating element even once it’s turned off – since this is the idle temperature, the tolerance was adjusted to take that into account. Furthermore, with just temperature as the variable, the peaks of the pink line asymptotically decrease implying that the frequency of the peaks increases as idle time increases; therefore, the relay switch (and heating element) would need to turn on and off at a very fast pace, damaging the components. With the tolerance increased to ±20% (green line), though the asymptotic behaviour is mitigated, there variation in the peaks would still need to be addressed. Longer testing times may have revealed more information with regards to the variation and decreasing values of the peaks. Finally, the frequency of the peaks also decreased – in Figure 17, the first trough of both lines are aligned showing that the larger tolerance stretches out the time between each heating cycle.

Figure 17: Line graphs of water temperatures at idle temperature using only temperature as control parameter. The two tolerances shown in the figure are for ±2% (pink) and ±20% (green). In the 2 hour experiment, the higher tolerance showed less asymptotic behaviour between its peaks and had a longer duration between each peak.

Therefore, by adding a time delay parameter, such that the temperature sensor remains on for two extra seconds after the threshold has been met, can decrease the disparity between these times – an updated control diagram is shown in Figure 18.


Figure 18: Updated control diagram for water temperature. When the conditions from the previous controller is met, the heater remains on for an additional 2 seconds to address the asymptotic behaviour.

In Figure 19, the additional red (±5%) and grey (20%) line highlight the improvement of using a time delay. The initial peaks of the lines vary due to differing start temperatures – a colder water tank would lead to a larger initial overshoot – therefore the lines on the graph have been aligned at their first troughs.


Figure 19: Line graphs of water temperatures at idle temperature using both temperature and time as control parameters. The four tolerances shown in the figure are for ±2% (pink), ±20% (green), ±5% (red), and +20%, −0% (grey). In the 2 hour experiments, the higher tolerance, time delayed parameters improved the performance of the controller. The lines have been offset so that the first troughs are aligned.

The line graph itself is difficult to analyse. In Table 2, information on the peaks of each line is written with the exception of the first two peaks of each graph (due to the offshoot explained above). By comparing the time difference between each peak (and taking an average), it is clear from the last row that adding a large tolerance and time parameter in the control allows for a longer duration between when the heating element is triggered. Furthermore, when comparing the difference between the max temperature of each peak (absolute value is used as sometimes the difference may be negative), the lowest difference and standard deviation is also seen by the high tolerance, time delayed controller.

Difference of Peak Times | Difference of Peak Temps
Parameters | Mean | Standard | Absolute Mean | Standard
Tolerance | Time delay | | Deviation | | Deviation
± 2% | none | 972 sec | 17.0 sec | 0.523 | 0.310
± 20% | none | 1187 sec | 81.2 sec | 0.570 | 0.301
± 5% | 2 sec | 1180 sec | 45.1 sec | 0.378 | 0.274
+20%, −0% | 2 sec | 1370 sec | 23.2 sec | 0.0600 | 0.0351

Table 2: Table with information on the means and standard deviations of different water heating control parameters. By comparing these values, a clear improvement can be seen from the +20%, −0%, time delayed controller, with least variance and stable peaks.

When the user requires chai to be made, the water is then heater from its idle temperature to 96◦C, per

the technical specifications. Figure 20 shows the temperature rising accordingly when a button is pressed at time, t = 18s, and takes approximately 90 seconds to heat up, meeting the specification. Though this initial test was conducted to ensure that the specification was met, it should have been repeated multiple times to make sure that they are reliable.

In this test, the heating element is switched off at 90◦C as the remnant heat is able to make the temperature rise to 96◦C. For the test, the Arduino was programmed to reheat the temperature of the water to 96◦C, though this would normally not happen as the water only heats up to the chai temperature once

when chai is being made. The Arduino was not able to both trigger the heating element and pump water at the same time, showing that the Arduino cannot conduct two operations, continuously, at once. This posed a problem for the milk heater, discussed in Section 4.5.

Figure 20: Line graph of the temperature of water after heating to chai temperature and then pumping 180mL out. The water is heated up in 90 seconds to the right temperature, meeting the technical specification. The Arduino was programmed in this experiment to reheat the water though normally the water would then return to its idle state.

### 4.3.4 Pump

The pump selected for this machine is also re-purposed from a Keurig. There are a number of reasons for this: the pump did not need to handle hot water, therefore eliminating that requirement; the compatibility of the size tubing from the reservoir and the water tank; and the flow rate, see Table 3, allowing for the timely transfer of the water, as per the specification.

The pump is voltage controlled, rated at 12V. As the Arduino cannot and does not need to drive this level of voltage, the IRLZ14 NPN MOSFET (see Appendix E) is used that has a gate to source trigger voltage of less than 5V, i.e. the maximum output of the Arduino. The circuit diagram for this is shown in Figure 21.


Figure 21: Schematic of the pump control. The pump is driven by an external voltage source that is controlled by the IRLZ14 using the Arduino. A red LED (YSL-R531R3D-D2) is also attached to the circuit as a visible verification method for the circuit.

The flow rate was determined by pumping cold water for 12 seconds into a jar on a scale 20 times since 1 gram of water equals 1 mL. The flow rate was determined to be 11.9 mL s⁻¹
. Therefore, the time for
pumping 180 mL is t = 15.1 s. However, the volume of water when testing with hot water did not correspond to 180mL, showing that the flow rate is affected by temperature..

The test was conducted again with hot water and the results are in Table 3. The hot water in the experiment is when the temperature is set to the chai temperature, 96◦C, and the cold water is room temperature, approximately 16◦C.

| Water Temp | Mean (mL) | Standard Deviation (mL)
1 | room temp (16◦C) | 140 | 0.2
1 | chai temp (93◦C) | 177 | 4.0
2 | | 178 | 5.4

Table 3: Data from water pumped out of the water tank. In each experiment, the water was pumped for 12 seconds and its mass (ergo volume) was measured 20 times.

The flow rate is therefore 14.9mL s⁻¹
. The results show that the amount of water pumped, in account to the standard deviation, fit within the tolerance of the amount of water required. There is a significantly larger standard deviation with the hot water than with the cold. From observation, when the water reached boiling temperatures, a few millilitres of water would drop into the container. A possible solution would be to add a pressure valve, ensuring that the water leaving the tube is only due to the pressure formed by the pump while also ensuring that the pressure can be maintained by the pump (possibly alterning the flow rate) and the water tank (causing it to explode), see Section 5.

Water Storage and Electrodes for Water Sensing

The machine stores water in a 2L removable reservoir, which was reconfigured from a used Keurig. This is as the reservoir comes with a stand and valve at the bottom, making sure that water does not leak. The valve attached to two tubes, one to the pump and the other to electrodes that sense the presence of water. Figure 22(a) show the reservoir on its stand and the water sensing electrodes taped upright to the side of the device.


(a) (b)

Figure 22: Images of (a) the water reservoir and its volume-checking electrodes and (b) cable at the top of the tank soldered to the electrode inside the tank. The electrode in (a) is aligned vertically so that the water can only reach them if the reservoir has 200mL in it, detecting a high signal, an error is presented otherwise (prompting the user to fill up the reservoir). The electrode in (b) detects if water has reached the top of the tank, detecting a low signal, otherwise the pump is triggered until the tank is full.

The machine needs to verify that there is water in two places: in the reservoir and the top of the tank. The former ensures that there is enough water to pump out the required amount of water to make chai, 180mL. The latter is to ensure that when 180mL of cold water is pumped in, 180mL of hot water is displaced out since if the tank is not full to the top, no water will be displaced until that point has been reached, see

Figure 23. If there is not enough water in the reservoir or the reservoir in not attached, the electrode will not detect a signal, thus prompting an error. If there is not enough water in the tank – which would typically only be when the machine is first set up (since the tank would be empty) or if the machine has not been used in a significantly long time for water to evaporate through the tube – the pump is triggered until the tank is full.

(a)

(b)

Figure 23: Illustrations of (a) not enough water for electrode 2 to be triggered, therefore (b) the pump transfers more cold water until the tank has been filled.

The reservoir electrode is active high. As shown in the schematic in Figure 24(a), the red cable in Figure 22(a) is attached to 5V and the blue cable is attached to the Arduino and ground. When water is present, the connection is shorted, allowing the Arduino to detect a signal, shown in Figure 24(b).

(a)

(b)

Figure 24: (a) Schematic of the reservoir electrodes and (b) graph of the voltage output from the electrodes before and after water is in contact from the reservoir. The dotted line represents the threshold that needs to be met in order to avoid false readings.

The water tank electrode is active low. The tank itself, as explained in Section 4.3.2, is connected to earth ground; when water fills the tank up, the Arduino would read 0V. Hence, the default reading into the Arduino is 5V. No data was attained for this due to lack of time. To test this, water would have been removed from the water tank to trigger the code that checks for this and a script to collect serial data would be run on MATLAB.

Figure 25: Schematic of the electrode attached to the water tank. This electrode is active low since the water tank is already earth grounder. The default input to the Arduino is 5V.

### 4.4 Ingredient Dispenser

The design of the dispenser takes into account: dispensing ingredients with the tight tolerances, provided in Section 2.3; sealing the ingredients away from steam entering the dispenser; and the ability for the user to store a large quantity of the ingredients inside the machine avoiding the user from having to replenish them frequently.

### 4.4.1 Dispenser Design

The dispenser, as shown in Figure 26, is a sphere with segment that has the volume (ergo mass) required for each individual ingredient. This also allows the strength of the chai to be increased by allowing multiple rotations of the same ingredient – see Section 5. The following calculation generalises the approximate number of segments each sphere would need – both the mass and density of the ingredient are required for this calculation. Figure 26 provides the labels used in the calculations.


(a) (b)

Figure 26: A (a) top and (b) front view of the rotator. The thickness of the edge of the spokes and the number of spokes determine the amount of each ingredient being dispensed. The gap in between each spoke is to fit silicone, which acts as a seal.

N =

Vsphere − N(Vsegment − Vdouble counted bottom) − Vprism

Vingredient

N =

Vsphere − Vprism

Vingredient + (Vsegment − Vdouble counted bottom)

N =

[

4/3 πr³

sphere] − [lengthπr²
prism]

mingredient

ρingredient

+ ([thickness ·

1/2 πrsegment] − [height · thickness · length])

Some measurements in these calculations are kept constant, for example, the radius of the PVC pipe is

9.53mm (0.375 inch), therefore:

N =

[

4/3· π · (25.4mm)

3
] − [(50.8mm · π · (4mm)

2
]

mingredient

ρingredient

+ ([thickness ·

1/2 π(25.4mm)

2
] − [25.4mm · thickness · 50.8mm])

The density of each ingredient was then calculated (the method is listed in Appendix D.2) and the final size for each dispenser is listed in Table 4.

Ingredient | Density | Spoke | Ncalculated | Nf inal | Actual Mass
| (g mm⁻³
| ) | Thickness (mm) | | | Dispensed (g)
Sugar | 1.59 × 10⁻³ | 3.81 | 5.05 | 5 | 7.52
Tea Leaves | 4.77 × 10⁻⁶ | 6.10 | 0.14 | 4* | 0.28
Cardamom | 4.70 × 10⁻⁴ | 5.08 | 10.58 | 10 | 1.18
Fennel Seeds | 5.35 × 10⁻⁴ | 4.83 | 11.44 | 11 | 1.07

Table 4: Calculations for the number of spokes required for each ingredient. The spoke number calculated is not an integer therefore by rounding N, the approximate actual mass dispensed is calculated. These masses remain within the tolerances specified in Section 2.3.

Table 4 lists N=0.14 for the tea leaves as the density of the leaves is two to three orders of magnitude smaller than the other ingredients. Therefore, a 4 spoked dispenser is designed as this is the minimum number of spokes required for the dispenser to form a seal within the PVC pipe.

The spokes were then fitted with semicircular silicone using the residual food-safe adhesive from the water heater (see Section 4.3.1).

### 4.4.2 Dispenser Design Changes

When initially designed, the dispenser’s radius was as close to the radius of the pipe, as shown in Figure 28(a), accounting for residual differences due to the 3D printer. As the silicone, however, had little space to flex, it generated a lot of friction against the pipe and did not move. The radius of the spokes was reconsidered to be approximately two thirds their original length, giving more surface area to the silicone sheets while retaining a seal that does not allow steam in or ingredients out when the dispenser is not being rotated.


(a) (b)

Figure 27: An (a) inside view of the original dispenser (without the silicone attachments) and
(b) the evolved final dispenser (far right). The larger silicone flaps allow a seal to be maintained without causing friction with the pipe.

The spherical dispenser has an extruded cut for a hex rod to force fit through it (once it is placed inside the pipe) and connect to the servo with a 3D printed hex rod attachment. The servo is secured to the pipe using a 3D printed, CAD designed, clamp, as shown in Figure 28. The pipe and hex rod were bought cut to size.


(a)

(b)

Figure 28: (a) Blown view of the SolidWorks designed ingredient dispensing subsystem, the bolts are not shown. (b) Image of the final fennel seed dispenser. The dispenser, clamp, and servo attachment were 3D printed using food safe PLA.

### 4.4.3 Results

Tests were conducted to collect data on the accuracy of the dispensers in order to make sure that the specifications were met. Due to time constraints, the sugar dispenser was not tested. Each dispenser was placed above a digital weighing scale and was programmed to spin at a specific angle repeatedly, with a delay between each rotation to give time to record the mass, in order to take 20 readings. The continuous servo (SM-4303R – see Appendix E) provided enough torque to spin the dispenser however cannot be programmed to rotate at a specific angle, rather a specific time. The rotation speed is 60
54 = 1.11 rounds per second.

The angle of the rotation was originally predetermined as each dispenser would dispense exactly the amount in the segment. For example, as listed in Table 4, the cardamom dispenser has N= 10spokes, therefore its angle should be 360

10 = 36◦
; however, this was not the case.

The cardamom dispenser has 10 spokes, therefore a rotation angle of θc =

360

10 = 36◦ was applied. Figure 29 shows the results for the cardamom. A 36◦
rotation resulted in a range of masses, between 0g and 2g, to be dispensed. The mean for this test was 0g as the success rate, i.e. the percentage of times that a non-zero mass was dispensed, was 40%. Decreasing the angle to 30◦ decreased the range by half, increased

the mean (though not within the tolerances in the technical specifications). Furthermore, the yield rate increased to 67%. Through observation it was discovered that since the dispenser rotates in one direction, the fine cardamom clumps together on one side of the pipe. This means that more force is required from the servo to rotate and that the density of the cardamom increases as it is being squashed together on one side. The solution to this is to have the servo jerk backwards, allowing the cardamom to redistribute in the pipe, shown in Figure 30. Though this increased the range again, the mean and the interquartile range fell within the tolerance listed in Section 2.3.

Figure 29: Box plot of the mass distribution from the cardamom dispenser. Decreasing the angle of rotation decreased the 0 yield rate of the dispenser and adding a jerk motion brought the mean and interquartile range within the tolerance for making chai.


Figure 30: Screen capture of video during one of mass tests showing uneven distribution of cardamom. The constant rotation of the dispenser in one direction leads the cardamom to become unevenly distributed, seen on the left side of the pipe.

The fennel seed dispenser has 11 spokes, therefore each spoke has an angular displacement of approximately θf =

360

11 ≈ 33◦

. Due to the experience with the cardamom dispenser, a larger angle, 60◦ , was
tested first. The range was just above 2g and, though the mean was close to 0g, the success rate was 78%. Decreasing the angle to 45◦
increased the success rate to 88% and brought the range closer, though the mass yield from each rotation remain low. Finally, with a 36◦
, the range once again increased but the yield rate became 100%, with no rotation resulting in a 0 yield and the mean moved closer to the desired level of 1g. Unlike cardamom, which is finer and can ’clump’ together, the fennel seeds (with its higher density) could not be jerked back to redistribute; however, adding a 30◦
tilt to the pipe itself allowed the seeds’ weight to redistribute the fennel seeds. This test was done by holding the dispenser as shown in Figure 32 – a vertical sheet marked 30◦
is not shown in the image. The success rate remained 100% with the tilt and tightened the range of the mass dispensed but brought the mean to 1.3g, missing the specification by being above the upper tolerance of 1.2g. Reducing the rotation angle further to 33◦ would have improved this as 36◦ angle

may have caused excess fennel seeds to dispense.


Figure 31: Box plot of the mass distribution from the fennel seed dispenser. The increased mean with changing the angle highlights a decrease in the number of 0 yields; adding a tilt to the dispenser itself allow the seeds to redistribute, therefore decreasing the variation in the results – both of which bring the mean dispensed ingredient to within the range for the technical specifications.

Figure 32: Image reenacting how the fennel seed test with 30◦
tilt occurred. In the actual test, a vertical sheet was placed behind the pipe marked with a 30◦ angle to ensure. Note: the dispenser shown in the image is filled with cardamom, the test did occur with fennel seeds.

A modified, angled clamp was designed for the fennel seed dispenser so that the pipe does not interfere with the rest of the dispensers, as shown in Figure 33. The hole for the hex rod would remain in the centre of the clamp so that the servo is attached in the same position. This was not 3D printed or implemented due to time restrictions.


Figure 33: SolidWorks model of the modified clamp. The pipe would slide in at a 30◦ angle while still meeting its centre hole (for the hex rod and servo) at the centre of the clamp.

The tea dispenser, as listed in Table 4, has 4 spokes, giving a rotation angle of 90◦
. This angle corresponds
to 0.28g of tea leaves being dispensed, therefore the dispenser is triggered 2 0.28 ≈ 7 times, equivalent to 630◦ or 1.75 rotations. The results for different angles of the tea do not indicate success for the technical

specification. Since the tea dispenser relies more on number of rotations rather than changing the angle of rotation, changing the angle did not greatly improve the results. The success rates were all 100% as the dispenser rotated multiple times for each test. The 90◦
test highlights the vast spread of the dispenser due to leakage of leaves in between each rotation, giving certain rotation up to 6 grams of tea and leaving others with nothing to dispense. Reducing the angle to 72◦ did not significantly alter the results. Increasing the angle to 100◦ did increase the mean, yet failed to address the spread of the results and meeting the technical

specification of 2 ± 0.4g of tea leaves.

Figure 34: Box plot of the mass distribution from the tea dispenser. The angles should be multiplied by 7 to correspond to the total angle of rotation. The plot shows a significant variation in all three of the results due to the leakage problem as well as a large proportion of 0 yields, when nothing is dispensed on a rotation.

The problem, as observed from the initial test with 90◦
, is the leakage of ingredients due to the 4 spoke design. As illustrated in Figure35(a), between each rotation, leaves would be able to leak, altering the mass and increasing the variance of the results. In future iterations, by doubling the number of spokes, the dispenser still only need to rotate 1.75 revolutions, though without leakage.

(a) (b)

Figure 35: (a) Illustration of tea leaves dispenser with 4 spokes and (b) a dispenser with 8 spokes at initial position and when rotated 45◦
. The 4 spoked dispenser leaves gaps on both sides between each rotation, whereas the 8 spoke dispenser always has a spoke sealing the edge.

The dispensers were then bolted onto the machine’s laser cut frame board, shown in Figure 36. The funnel was not built for the prototype due to time constraints.


Figure 36: The tea leaves, sugar, cardamom, and fennel seed dispensers attached to the frame of the machine. The 3D printed clamps have bolt holes and counter sinks, which align with the laser cut board. The funnel was not built due to time constraints.

### 4.5 Milk Heater

### 4.5.1 Heater Selection

As the user inserts the milk in a carafe into the machine it needs to be safe for the user to handle. A traditional immersion heating element can reach hundreds of degrees, deeming unsafe for a user to be exposed to it and burning the milk. Milk is a complex mixture of water, fats, and proteins; with a heating element, the fats and proteins will separate out from the water when heated, and form a layer on top. This layer prevents the water from evaporating and the continued heat causes compounds to stick to the bottom. An induction heater, which only transfers heat to an inductive plate – in this case, a 4 inch stainless steel, 480mL saucepan – is used instead.[14] Typical induction heaters available on Amazon are equipped with fans to make sure that the base plate does not heat up significantly enough to burn the user and can recognise if the pan is removed from the heater, flagging an error.[15, 16]

Initially, AmazonBasics 1800W induction cook top was selected for its size (its length being 33cm – below the 50cm technical specification), power output, and compatibility with the 4 inch carafe. The cook top was tested to make sure that the milk heats up within the time specified by the technical specifications, which it does, graphed in Figure 37. Approximately 100mL is added to the carafe, placed on the cook top and the cook top is powered to its maximum ”power” setting of 1200. The temperature data was collected using a infrared sensor at a rate of 1 per second. The variation in the data is attributed to the this, which would have been improved on by using an immersed thermocouple sensor, like the tests conducted for the water heater.

Figure 37: Line graphs of the temperature of milk over time using the ”1200 power” setting on the induction heater. Test 1 is offset to align its initial temperature with Test 2. The noise in the data is attributed to the positioning of the infrared temperature sensor used to take recordings.

Both tests in Figure 37 do conclude that the milk can be heated to 80◦ within the time frame indicated

in the recipe and technical specifications.

### 4.5.2 Controlling Induction Heater

The AmazonBasics cook top is fitted with two control circuits: the user interface with pushbuttons and a digital number display, and an internal controller. Since there are internal controls for sensing the presence of a saucepan on the cook top and for temperature, the Arduino was programmed to replicate the code sent to the internal controller using the interface’s asynchronous transmit and receive protocol – this needs to be decoded first. The user interface controller, viewed in Figure 38(a), is connected to a 2000W power isolation transformer as the cook top is not earth grounded, which could cause a short due to the potential difference between the floating ground of the induction heater and the earth ground of the oscilloscope.


(a) (b)

Figure 38: Images of (a) the user interface controller connected to the oscilloscope and (b) bits read from the TX pin of the controller. The cook top does not have an earth ground cable hence it is plugged in through a 2000W power isolation transformer (grey box in top left) to avoid it from shorting. The bits are continuously sent in a loop at a baud rate of 9600 bits per second.

The oscilloscope, as shown in Figure 38(b), was set to trigger on the first rising edge of the signal, which is otherwise displayed to loop itself. Each bit is has a time width of 104µs and each signal is comprised of 100 bits, giving a time cycle of 10.4ms. The signal is comprised of 10 bytes, with each byte having a start bit, 0, and stop bit, 1, address. By pressing the following sequence of buttons, the induction heater enters its maximum power output capability and then it’s minimum power output:

- ’Start/Stop’
- ’Temp.’
– Max power output
- ’−’ five times
– Min power output

The TX readings do not correspond each button press in the same sequence. For example, if the temperature setting is turned down by pressing ’−,’ from 400◦F to 300◦F, the signal transmitted will remain the same until the temperature of the carafe has reached 300◦
, at which point the induction heater would switch off or enter an intermediate heat state. This means that the induction heater is not continuously varying its temperature, rather following a 3 tier hysteresis control. The following states, relevant to the sequence above, are transmitted by the controller:
- Off
– When the controller is plugged in
- Standby
– When the ’Start/Stop’ button is pressed

- Induction heater on
– When the ’Temp.’ button is initially pressed, entering the highest temperature setting
– When the temperature of the base plate falls below the temperature displayed on the digital number display
- Induction heater off
– When the temperature of the base plate exceeds the temperature displayed on the digital number display
- Induction heater intermediate on
– Assumed to be when the temperature of the base plate is within a tolerance of the temperature displayed on the digital number

See Appendix D.4 for the signals for each state and their decoded hex values.

The Arduino is able to transmit asynchronous 8-bit signals, defaulting with a 0 start bit and 1 end bit; however, the Arduino does so by sending them right to left rather than left to right. For example, 0x0A corresponds to 00001010 but on an oscilloscope, the Arduino’s output would be 01010000. Figure 39 represents the altered binary bytes in decimal.


Figure 39: Graph of the bytes (in decimal) transmitted by the original controller (blue) and by the altered code sent by the Arduino (orange). The 10 bytes of code are sent in 10.4ms.

These signals would then be used in alignment with the times from the tests shown in Figure 37 to determine how much and how long the milk should be heated. Should time restrictions not have been an impedance, the following tests would have been carried out to conclude the milk heater subsystem: while timing the entire process, using the induction heater, the milk would have been brought to its boiling point, triggering the intermediate on state; the ingredients would have been inserted into the carafe, followed by the water. The concoction would be monitored to determine if the intermediate on state is able to provide sufficient heat or if the fully on/off state need to be triggered.

### 4.5.3 Determining Presence of Carafe

When the user presses the button to make chai, the machine has to verify if the carafe has been placed in the machine. Data was also collected from the RX pin of the user interface controller as when nothing is placed on the base plate an error, ’E1’, is displayed. The bits fluctuated very rapidly, not allowing the oscilloscope to latch onto the signal, thus there is no data to determine the code that would be displayed when the saucepan is not placed onto the plate. Alternate methods for verifying this as well as checking if the carafe has milk inside it are discussed in Section 6.

## 5 Final Prototype and Conclusions

This senior design project presents The Perfect Chai Maker that was concluded three weeks early due to complications related to the COVID-19 pandemic. As a result, much of the verification stage for the final subsystem and the integration stage were not completed, seen in Figure 40.

Figure 40: Final prototype of The Perfect Chai Maker. The image is missing the induction heater, Arduino, and carafe, and the servo wires are disconnected since the Arduino was removed.

To analyse the performance of each independently working subsystem, the technical specifications are revisited in Table 5. The attained (or average, if applicable) value and their tolerances (standard deviations) are listen. If the attained value is within the tolerance of the target value, it is marked green; if the value was not tested but predictably could have been attained, it is marked orange; if the test failed to achieve the target value, it is red.

Specification | Target
| Value | Tolerance | Attained
| | | Value | Attained
| | | | Tolerance | Units
| | Process
Time to make chai | < 5 | Inferred | mins
Pump: Hot water is transferred
from the water tank to the mix- ing container | 180 | ±15 | 178 | ±5 | mL

Controller: Maintenance of idle
temperature when machine is not in use | 50 | +5 | 52 | ±2 | ◦C

Time taken to raise milk and wa-
ter temperature | 120 | −0
| | +10 | water: 90,
| | | milk:75 | water: n/a,
| | | | milk: ±5 | secs
| | Ingredients
Temperature of water when mak-
ing chai | 96 | −4
| | +1 | | | ◦C

Temperature of milk when mak-
ing chai | 80 | −0
| | +5 | | | ◦C

Dispense:
Tea leaves | 2 | ±0.4 | 3.9 | 3.5 | g
Sugar | 8 | ±2.0 | Inferred | g
Cardamom | 1 | ±0.2 | 1.0 | 0.4 | g
Fennel seeds | 1 | ±0.2 | 1.3 | 0.3 | g
| | Other
Device Size | 50x50x50 | 47x33x50 | cm³

Table 5: Technical specifications for the implementation of The Perfect Chai Maker. Using the recipe and testing, the specifications for the build of the machine were formed. Green rows are specifications that were met, orange are inferred to have been met, and red were not met.

The sugar dispenser had not been tested but from the iterations on the cardamom and fennel seed dispenser, testing would have probably resulted successful. Moreover, there is greater leeway with the amount of sugar dispensed due to the larger tolerance, which from Figure 29 and 31, the dispenser is capable of dealing with.

The time to make chai was also not tested owing to the subsystems not being integrated. Each subsystem, though, was designed to operate independently and simultaneously, and showed to complete their tasks within their allocated times. Thus, it can be inferred that the machine would indeed have followed the chai recipe and made chai in under 5 minutes.

## 6 Future Development

There are many places improvements that can be made to the machine to ensure that it is a useful and versatile product for the user. This includes additional hardware design or software features, as well as testing the machine to debug errors and ensure reliability.

### 6.1 User Interface and Customizability

The machine is currently controlled by one button that triggers it to simply make one mug of chai. The machine was designed with the capability to alter the strength of the chai, which is controlled by the dispenser. The first solution to this is to add multiple buttons, each indicating a different strength, which corresponds to the number of rotations made to the dispensers. Furthermore, a screen and a jog wheel/button layout can allow the user to be specific about the strength. This would, in turn, require the dispensers to divided into even finer segments than they are currently at, as well as have a tighter tolerance in order to deal with the specificity, see Section 6.2

The machine’s current form of design is capable of producing more than one mug of chai due to the large induction heater, which can fit a larger saucepan, and the volume of water that the machine can hold, approximately 2.8L. By having an interface, the user could also select the amount of chai they want to make. Similar problems that were posed in Section 4.5.3 would be present in this case, which are discussed in Section 6.3.

### 6.2 Ingredient Dispenser

First of all, the tea leaves dispenser requires to be redesigned and tested to ensure that the issue of leakage was dealt with and that the variance with the results shrunk. The sugar dispenser also needs to be tested to verify that technical specification is also met.

One of the issues with the continuous rotation servo is that there is no feedback to determine the angle that the servo has turned, adding to the error in the results. By adding a sensing device, such as a switch that is flicked by the servo arm or a hall effect sensor that detects the proximity of the bolt inside the servo arm, every half revolution can be taken into account for how much the dispenser is spinning (since the arm has two sides).

The ingredient dispensers were designed with specific ingredients in mind that have different densities and granularities. Because of this, the dispensers are not flexible and the user cannot replenish, for example, the cardamom dispenser with cinnamon instead. The user could, first, be shipped dispenser pipes – the modular setup would allow the user to replace the pipes for their desired ingredient. Alternatively, the dispensers can be filled with different combinations of spices, rather than individual spices, which are distributed (sold) by the ”manufacturer.” This allows a regular income similar to the business models of the pod-based machines described in Section 1.3.

An alternative method of dispensing ingredients could also be explored, for example an auger conveyor.

The ingredients would not need to be sealed as they would be dispensed from the top of a pipe rather than the bottom, therefore no steam can penetrate in and the ingredients won’t be able to fall out. Furthermore, the auger would not need specific designs for each ingredient, allowing it to be universal. This would require the pipes to be placed closer to the bottom of the machine so that they do not protrude more than already, illustrated in Figure 41. Furthermore, a different servo mount would need to be designed since the servo would sit at the base of the pipe rather than along its side.

Figure 41: Illustration of an auger/conveyor lift placed at a lower height. This would ensure that the pipes are reliably dispensing into the carafe.

### 6.3 Milk Heater

The possibility of customising the volume of the drink, discussed in Section 6.1 poses the question of verifying the volume inserted by the user. The current carafe has labels marking the recommended volume of milk that should be inserted, but what if this level is not met or no milk is inserted at all? The current design would still heat an empty carafe for 90 seconds until the water is inserted. By adding a weighing scale underneath the base plate, which can accurately measure the weight being put on the base plate, this problem can be solved. If a larger saucepan is used, as suggested in Section 6.1, the machine would not recognise if the larger weight is due to the milk or the saucepan. The alternate solution is to store the milk inside the machine using a removable reservoir, allowing it to be stored in the fridge when not used as to avoid the milk from going bad. The milk would damage a normal water pump, instead, as illustrated in Figure 43, the pump can pump air into the reservoir, pushing the milk out from the bottom.

Figure 42: Illustration of the air pump pushing milk (indicated in grey) out of the bottom of the reservoir by pushing in air.

This setup causes the problem of cleaning products to arise. Since the milk is poured in cold, it decreases the chance and frequency of mold developing. This reservoir should have detachable tubes, similar to the Nespresso Latisima, see Section 1.3, so that they can be washed by the user.

### 6.4 Micro-controller

The Arduino was compatible with all the devices used in this machine. Further testing with the milk heater, however, would have revealed that that the Arduino would not be able to send a continuous string of bytes to the milk induction heater (which it requires) while also simultaneously communicating to the servos and water heating element. The concern is that once, for example, the servo is activated, the code transmitting the TX signal would no longer be run – making the TX signal go flat – causing the induction heater to reset to the off or standby state. A more complex finite state machine or, alternatively, a micro-controller that can continue running commands while focusing on a different task would solve this issue.

## 7 Acknowledgements

First and foremost, I’d like to thank my mentors. My thesis advisor, Dr Nathan Taylor, stepped in to provide help and advice even before officially signing up to be my advisor. Nathan’s support, reminders, and critiques ensured that my project was being completed to the best of my ability. Without taking my first engineering class, ES51, with Nathan freshman spring semester, I would not have been as excited about engineering as I am today. My thesis section leader, Nishant Sule, has been the kindest, most patient, and dedicated not-engineer SEAS has. Nishant’s attention to the details in everyone’s project in our section and his ability to make us think critically as well as bounce ideas off each other was inspiring.

I’d also like to extend my thank yous to Evan Smith, Benjamin Brown, and Jim MacArthur, for making themselves available whenever I needed and answering my stupidest questions humbly and with patience. Without Evan and Ben, I would have electrocuted myself while working on the induction heater. Without Jim, I would have electrocuted myself assembling the water heater.

I’d like to thank my family and friends who have been a constant source of motivation for this project. I have been filled with love to see so many people interested in my project and hoping for its success. Thank you to Prasidh for reminding me everyday if it ’is making chai yet.’ Needless to say, it is not. Lastly, I’d like to thank my parents for teaching me all I know about my culture – me drinking my father’s chaa, made every morning, was integral to my routine most of my life.

To everyone, I promise to bring you a cup of chai produced by this machine.

# Appendices

## A Bill of Materials

Name | Vendor | Price | Quantity | Subtotal
Arduino Mega 2560 R3 | Adafruit | 28.50 | 1 | 28.50
Soft PVC Clear Tubing, 3/8” ID, 9/16” OD | McMaster | 34.50 | 1 | 34.50
Waterproof temperature Sensor DS18B20 | Adafruit | 14.95 | 1 | 14.95
EP750 Adhesive | Ellsworth | 30.30 | 1 | 30.30
AC Wall Adapter, 12V-1A | Digikey | 8.95 | 1 | 8.95
480mL, 4 inch saucepan | Amazon | 16.99 | 1 | 16.99
Standard-Wall Clear Rigid PVC Pipe for Water, Size
2, 2 Feet Long | McMaster | 24.64 | 2 | 49.28

Food-Grade High-Temperature Silicone Rubber
Sheets and Strips | McMaster | 22.30 | 1 | 22.30
Davidson’s English Breakfast Tea, 0.45g | Amazon | 12.83 | 1 | 12.83
Simply Organic Cardamom, 80g | Amazon | 4.59 | 1 | 4.59
Simply Organic Fennel Seeds, 54g pack of 2 | Amazon | 3.99 | 1 | 3.99
AmazonBasics 1800W Induction heater | Amazon | 49.97 | 1 | 49.97
Unused Items | | | Total | $ 255.74
Servo TowerPro SG-5010 | Adafruit | 12 | 4 | 48
Contact-less Infrared Thermopile Sensor Breakout -
TMP006 | Adafruit | 9.95 | 1 | 9.95
Relay Switch Kit - KIT-13815 | Digikey | 8.95 | 1 | 8.95
Adafruit 16-Channel Servo Driver - PCA9685 | Adafruit | 14.95 | 1 | 14.95
JQX-15F Relay Switch | Sparkfun | 2.95 | 1 | 2.95
Isiler 1800W Induction Heater | Amazon | 69.95 | 1 | 69.95
| | | Total | $434.85
Obtained from advisor
Keurig K-Cafe: KPM27D air pump, water tank, reservoir

## B Schematic


Figure 43: Final schematic of electrical components.

## C Arduino Code

#include <OneWire.h>

#include <DallasTemperature.h>

#include <Servo.h>

//define pins for each component

#define MAKECHAI 22

//button for starting chai process, digital input

#define TEMPSENSE 30

//temp sensor, digital input

#define PUMPDRIVER 47

//pump switch, digital PWM

#define WATERHEATERCONTROL 51 //relay switch for heating element

#define WATERPRESENT_TANK A2

//electrodes detect voltage for presence in tank

//- **pump water if not enough

#define WATERPRESENT_RESERVOIR A3

//electrodes detect voltage for presence in reservoir

//- **ERROR if not enough

//dispenser

#define CARDAMOM 8

#define FENNEL 9

#define TEA 10

#define SUGAR 11

//Induction heater transmission buttons//

const byte idleoff[] = {176, 79, 240, 15, 240, 240, 75, 15, 240, 240};

//when first connected to power supply, completely off

const byte idleon[] = {176, 79, 240, 60, 240, 240, 240, 150, 240, 240};

//turn machine on

const byte fulltemp[] = {176, 79, 30, 120, 180, 225, 240, 150, 240, 240};

//turn induction heater on to max setting

const byte halftemp[] = {176, 79, 90, 120, 180, 225, 240, 150, 240, 240};

//turn induction heater to in between state

const byte zerotemp[] = {176, 79, 240, 60, 180, 225, 240, 150, 240, 240};

//turn induction heater off

const int arsize = sizeof(idleoff); //size of array for serial.write

//initiate temperature sensor

OneWire oneWire(TEMPSENSE);

DallasTemperature sensors(&oneWire);

// create servo object to control a servo

Servo cardamomServo;

Servo fennelServo;

Servo teaServo;

Servo sugarServo;

float Celcius = 0;
int amount = 14896; //pump on for 14.89455 secs to pump 187 ml

//bool isFirst = false;

void setup(void)
{

Serial.begin(9600);

sensors.begin();

cardamomServo.attach(CARDAMOM);

fennelServo.attach(FENNEL);

teaServo.attach(TEA);

sugarServo.attach(SUGAR);

pinMode(PUMPDRIVER, OUTPUT);

pinMode(WATERHEATERCONTROL, OUTPUT);

pinMode(MAKECHAI, INPUT); //Press button, active low

pinMode(WATERPRESENT_TANK, INPUT);

pinMode(WATERPRESENT_RESERVOIR, INPUT);

Serial.write(idleoff); //set up stage for heater should be off }

void loop(void)
{

tempSense();

isWaterPresent();

if(buttonPressed() == true) //&& isWaterPresent()==true) {

heatMilk();

delay(300);

dispenseIngred(1);

delay(300);

switchPump(2);
}

// else if(buttonPressed() == true && isWaterPresent()==true){

// **SCREEN DISPLAYING LACK OF WATER
// }

delay(100);
}

bool isWaterPresent(){

int tankValue = analogRead(WATERPRESENT_TANK);

int reservoirValue = analogRead(WATERPRESENT_RESERVOIR);

//electrodeValue between 0-1023, input of 5V, therefore conversion required

float resVoltage = reservoirValue * (5.0 / 1023.0);

float tankVoltage = tankValue * (5.0 / 1023.0);

if(resVoltage > 0.7)
{

return true;
}

//DISPLAY ADD WATER

while(tankVoltage < 1)
{

switchPump(1);
}

switchPump(0);
}

bool buttonPressed(){

int buttonState;

buttonState = digitalRead(MAKECHAI);

int programState = 0;

long buttonMillis = 0;

const long intervalButton = 3000;

long ledMillis = 0;

const long intervalLed = 5000;

unsigned long currentMillis = millis();

if (buttonState == LOW && programState == 0) {

buttonMillis = currentMillis;
programState = 1;
}

else if (programState == 1 && buttonState == HIGH) {

programState = 0; //reset
}

if(currentMillis - buttonMillis > intervalButton && programState == 1) {

programState = 2;

ledMillis = currentMillis;

return true;
}

if(currentMillis - ledMillis > intervalLed && programState == 2) {

programState = 0;

return false;
}

if(buttonState == LOW)
{

return true;
}

return false;
}

void waterHeat(bool on){

if(on){

digitalWrite(WATERHEATERCONTROL, HIGH); }

else{

digitalWrite(WATERHEATERCONTROL, LOW); }

}

// SENSOR FOR WATER TEMPERATURE

//*********CALIBRATE**********//

void tempSense()
{

int idealTemp = 50;

int tolerance = 0.2;
sensors.requestTemperatures();

Celcius = sensors.getTempCByIndex(0);

if(Celcius < idealTemp - idealTemp*tolerance && Celcius > 0) {

waterHeat(true);

//TURN RELAY OFF = HEATER OFF }

else if(Celcius > idealTemp){

delay(2000);

waterHeat(false);
}

//Serial.println(Celcius); }

// HEAT MILK IN TANK //

void heatMilk()
{

//need to tap into controller settings to mess with this. }

// DISPENSE INGREDIENTS. STRENGTH DETERMINED ON SCALE FROM 1 TO 3. ASSUME 1 'TIL IMPLEMENTATION //

void dispenseIngred(int strength)
{

float servoSpeed = 1.11;
float cs = servoSpeed*(360/10);

float fs = servoSpeed*(360/11);

float ss = servoSpeed*(360/5);

float ts = servoSpeed*360/90;

cardamomServo.attach(CARDAMOM);

cardamomServo.write(180);

delay(cs);

cardamomServo.write(0);

delay(cs*3);

cardamomServo.detach();

fennelServo.attach(FENNEL);

fennelServo.write(180);

delay(fs);

fennelServo.detach();

sugarServo.attach(SUGAR);

sugarServo.write(180);

delay(fs);

sugarServo.detach();

teaServo.attach(TEA);

teaServo.write(180);

delay(fs);

teaServo.detach();

}

// PUMP WATER TO POT //

void switchPump(WATERPRESENT) {

int amount = 11781*5;

if(WATERPRESENT == 2)
{

digitalWrite(PUMPDRIVER, HIGH);

delay(amount);

digitalWrite(PUMPDRIVER, LOW); }

else if(WATERPRESENT == 1)
{

digitalWrite(PUMPDRIVER, HIGH); }

else
{

digitalWrite(PUMPDRIVER, LOW); }
}

## D Data Collection

D.1 Ingredient Tolerance Test

Mass (g)
| Cardamom | Fennel Seeds | Sugar | Tea Leaves
| 1 | 1.2 | 8.6 | 2.4
| 1.1 | 1.1 | 10 | 2.2
| 1.2 | 0.9 | 8.9 | 1.7
| 1 | 0.9 | 6 | 2.3
| 1.3 | 0.9 | 6 | 1.4
| 0.8 | 0.8 | 6.7 | 1.4
| 0.9 | 0.7 | 8 | 2
| 0.8 | 1 | 9 | 2.6
| 0.8 | 1.2 | 11 | 2.3
| 1.2 | 1.1 | 7.4 | 2
Standard Deviation | 0.19 | 0.17 | 1.67 | 0.41

Table 6: Test of measuring masses of ingredients using tea and table spoons. The standard deviations determine the tolerances for the technical specifications.

D.2 Calculating Ingredient Density

The ingredients’ densities were worked out by measuring their mass (directly) and their volume (indirectly). The Active Learning Lab space was not able to provide containers that are listed as being food safe. Therefore, the ingredients were kept in zipper storage bags. The bag would be filled around a third of the way and the air would be removed as the bag is being closed. The ingredients were not pressed on tightly as to ensure that they hold their density that would be maintained when they’re in any other normal container. After being weighed on a scale, the bag is submerged fully into a large jar of water and a line is drawn at the new water level. The bag is removed, water is filled up to the line and measured using a serological pipette. The advantages of using a serological pipette are that it is optically optimised, reducing the observer’s error, there is increased volume accuracy, and the clear ascending and descending graduation avoids spillage of water or droplets on the side of the jar being unaccounted for. Since the densities of the ingredients are very small, it was vital to ensure that these values are accurately obtained.

D.3 Dispensing Ingredients

Mass (g) of Fennel Seeds Dispensed with each Parameter
60 ◦ | 45 ◦ | 36 ◦ | 36 ◦ with 30◦
| | | tilt
0 | 2.2 | 0.5 | 1.1
0.8 | 0.3 | 1.5 | 1.3
0 | 0 | 0.6 | 1
0.3 | 0.2 | 1.7 | 1.22
2.1 | 2 | 0.8 | 1.5
0.3 | 0.1 | 1.5 | 1.4
0.1 | 0.1 | 2 | 1.44
0.3 | 0.3 | 2.1 | 1.9
1.6 | 0.1 | 0.6 | 1.9
0.4 | 0.1 | 2.6 | 1.32
0.2 | 0.3 | 1.7 | 1
2 | 2.1 | 1.9 | 1.21
0.3 | 0.3 | 2.1 | 1.1
0.2 | 2.1 | 2.2 | 2
0.5 | 0 | 2.2 | 1.1
1.4 | 0.3 | 0.9 | 1.3
0.3 | 0.4 | 1.4 | 1.06
0.2 | 1.3 | 0.6 | 1.6
1.6 | 0.4 | 1.7 | 1.5
0.9 | 0.1 | 2.1 | 1
0.1 | 0 | 2.2 | 1.7
0.5 | 0.1 | 0.5 | 1.9
1.7 | 0 | 1.5 | 1.23
0 | 0 | 0.6 | 1.2
0.3 | 0.1 | 1.7 | 1
1.8 | 0.2 | 0.8 | 1.8
0.6 | 0.1 | 1.5 | 1.1
0.1 | 0 | 2 | 2
0.6 | 0.2 | 2.1 | 1.1
1.4 | 0.4 | 0.6 | 1.3
0.1 | 0.5 | 2.6 | 1
0.3 | 0.6 | 1.7 | 1.66
1.8 | 0.1 | 1.9 | 1.43
0.3 | 0.5 | 2.1 | 1.23

0.3 | 0.6 | 2.2 | 1
1.9 | 0.4 | 2.2 | 0.98
0.4 | 0.4 | 0.9 | 1.9
1 | 0 | 1.4 | 2.2
0.5 | 0.1 | 0.6 | 1
1.4 | 0.5 | 1.7 | 1.8
0.3 | 0.6 | 2.1 | 1.1
0.2 | 0.2 | 2.2 | 1.7
1.6 | 0.2 | 0.5 | 0.93
0.9 | 0.4 | 1.5 | 1
0.1 | 0.8 | 0.6 | 2.2
0.5 | 0.6 | 1.7 | 1.7
1.7 | 0.1 | 0.8 | 0.95
0 | 0.1 | 1.5 | 1.9
0.3 | 0 | 2 | 1
1.8 | 0 | 2.1 | 2.8
0.6 | 0.1 | 0.6 | 0.97
0.1 | 0.1 | 2.6 | 1.1
0.6 | 0.4 | 1.7 | 2
1.4 | 2 | 1.9 | 0.97
0.1 | 0.5 | 2.1 | 1.3
0.3 | 0.6 | 2.2 | 0.94
1.8 | 0.6 | 2.2 | 1.6
0.3 | 1.9 | 0.9 | 1.5
0.3 | 0.1 | 1.4 | 1
1.9 | 0.1 | 0.6 | 1.7
0.4 | 0.1 | 1.7 | 1
0 | 1.8 | 2.1 | 1
0 | 0.5 | 2.2 | 1.2
0 | 0.6 | 1.7 | 1.4
0 | 0.5 | 1.9 | 1.8
0 | 1.9 | 2.1 | 1.1
0 | 0.5 | 2.2 | 1
0 | 0.6 | 2.2 | 1
0 | 0.1 | 0.9 | 0.9
0 | 0.1 | 1.4 | 0.8
0 | 0.1 | 0.6 | 1
0 | 1.2 | 1.7 | 1.3
0 | 0.4 | 2.1 | 1

Table 7: Data collected from repeating the fennel seed mass tests 70 times.

Mass (g) of Cardamom Dispensed with each Parameter
36 ◦ | 30◦ | 30◦ + 3*30◦
jerk
0 | 1 | 0.9
0 | 0 | 0.5
1 | 1.6 | 1.1
0 | 1 | 0.7
2 | 0 | 1.1
0 | 0.6 | 1.8
0.5 | 0 | 0.3
0.8 | 1.8 | 0
0 | 0.3 | 1.6
0 | 0.5 | 0.7
0 | 0.5 | 1.4
0 | 1.6 | 0.8
0 | 0.3 | 1.1
0.8 | 0 | 0.7
0.6 | 0.1 | 1.1
0.8 | 0 | 1.5
0 | 0 | 1.5
0.1 | 0 | 1.2
0.1 | 0.1 | 1.1
1.1 | 0 | 0.8
0 | 0.3 | 0.9
1.3 | 1.3 | 0.4
0 | 0.5 | 0.6
0 | 0 | 1.3
0 | 0 | 1.3
0 | 0.5 | 0.1
0 | 0.3 | 1
0.3 | 0 | 1.3
0 | 0.5 | 0.8
1.7 | 0.5 | 1.2

Table 8: Data collected from repeating the cardamom mass tests 20 times.

Mass (g) of Tea Leaves
Dispensed with each Parameter
90◦ | 72◦ | 100◦
0.3 | 0 | 4
4 | 1.5 | 1.5
0.2 | 4.2 | 4.2
0.2 | 0 | 7
0.2 | 0 | 4
0.7 | 0 | 3
4.5 | 5.1 | 5.1
0.5 | 0.2 | 0.2
0 | 0 | 5
0.5 | 0.1 | 0.1
4.9 | 3 | 3
0 | 5 | 5
0 | 0.2 | 0.2
5.9 | 5.6 | 5.6
0 | 0.2 | 0.2
0 | 0 | 4
0.6 | 0 | 7
4.7 | 1.7 | 1.7
0 | 4.8 | 4.8
0 | 0 | 5
4.3 | 0 | 6.3
0.2 | 0.4 | 0.2
0 | 3.5 | 6.9
4.8 | 0.3 | 7.3
0 | 0.1 | 3
0.1 | 0 | 5
1.5 | 1.4 | 0.2
3.6 | 3.7 | 6.8
0 | 0 | 0.2
0.2 | 0 | 3.3
4 | 0.2 | 0.2
0.2 | 3.7 | 3.7
0 | 0 | 7
4 | 0 | 2.5
0 | 0.2 | 4.3
0 | 4.3 | 4.3
3.1 | 0 | 3.9
0.2 | 0.1 | 0.1
4 | 0.2 | 0.2
0.2 | 2.8 | 2.8

Table 9: Data collected from repeating the tea leaves mass tests 40 times.

D.4 Induction Heater Signals

The induction heater’s signals, transmitted via the UI’s TX pin, have been listen below. The yellow highlights indicate changes between each set of data.

State: off
Start
bit | Data bits (one byte) | End
bit
0 | 0 | 0 | 0 | 0 | 1 | 1 | 0 | 1 | 1
0 | 1 | 1 | 1 | 1 | 0 | 0 | 1 | 0 | 1
0 | 0 | 0 | 0 | 0 | 1 | 1 | 1 | 1 | 1
0 | 1 | 1 | 1 | 1 | 0 | 0 | 0 | 0 | 1
0 | 0 | 0 | 0 | 0 | 1 | 1 | 1 | 1 | 1
0 | 0 | 0 | 0 | 0 | 1 | 1 | 1 | 1 | 1
0 | 1 | 1 | 0 | 1 | 0 | 0 | 1 | 0 | 1
0 | 1 | 1 | 1 | 1 | 0 | 0 | 0 | 0 | 1
0 | 0 | 0 | 0 | 0 | 1 | 1 | 1 | 1 | 1
0 | 0 | 0 | 0 | 0 | 1 | 1 | 1 | 1 | 1
Concat | Hex | Decimal | Concat opposite for
| | | Arduino | New
| | | | hex | New
| | | | | dec
00001101 | D | 13 | 10110000 | B0 | 176
11110010 | F2 | 242 | 01001111 | 4F | 79
00001111 | F | 15 | 11110000 | F0 | 240
11110000 | F0 | 240 | 00001111 | F | 15
00001111 | F | 15 | 11110000 | F0 | 240
00001111 | F | 15 | 11110000 | F0 | 240
11010010 | D2 | 210 | 01001011 | 4B | 75
11110000 | F0 | 240 | 00001111 | F | 15
00001111 | F | 15 | 11110000 | F0 | 240
00001111 | F | 15 | 11110000 | F0 | 240

Table 10: Table for the signals, their converted decimal and hexadecimal equivalents, and the desired Arduino code for Off State

State: Standby
Start
bit | Data bits (one byte) | End
bit
0 | 0 | 0 | 0 | 0 | 1 | 1 | 0 | 1 | 1
0 | 1 | 1 | 1 | 1 | 0 | 0 | 1 | 0 | 1
0 | 0 | 0 | 0 | 0 | 1 | 1 | 1 | 1 | 1
0 | 0 | 0 | 1 | 1 | 1 | 1 | 0 | 0 | 1
0 | 0 | 0 | 0 | 0 | 1 | 1 | 1 | 1 | 1
0 | 0 | 0 | 0 | 0 | 1 | 1 | 1 | 1 | 1
0 | 0 | 0 | 0 | 0 | 1 | 1 | 1 | 1 | 1
0 | 0 | 1 | 1 | 0 | 1 | 0 | 0 | 1 | 1
0 | 0 | 0 | 0 | 0 | 1 | 1 | 1 | 1 | 1
0 | 0 | 0 | 0 | 0 | 1 | 1 | 1 | 1 | 1

Concat | Hex | Decimal | Concat opposite for
| | | Arduino | New
| | | | hex | New
| | | | | dec
00001101 | D | 13 | 10110000 | B0 | 176
11110010 | F2 | 242 | 01001111 | 4F | 79
00001111 | F | 15 | 11110000 | F0 | 240
00111100 | 3C | 60 | 00111100 | 3C | 60
00001111 | F | 15 | 11110000 | F0 | 240
00001111 | F | 15 | 11110000 | F0 | 240
00001111 | F | 15 | 11110000 | F0 | 240
01101001 | 69 | 105 | 10010110 | 96 | 150
00001111 | F | 15 | 11110000 | F0 | 240
00001111 | F | 15 | 11110000 | F0 | 240

Table 11: Table for the signals, their converted decimal and hexadecimal equivalents, and the desired Arduino code for Standby State

State: Induction heater on Start
bit | Data bits (one byte) | End
bit
0 | 0 | 0 | 0 | 0 | 1 | 1 | 0 | 1 | 1
0 | 1 | 1 | 1 | 1 | 0 | 0 | 1 | 0 | 1
0 | 0 | 1 | 1 | 1 | 1 | 0 | 0 | 0 | 1
0 | 0 | 0 | 0 | 1 | 1 | 1 | 1 | 0 | 1
0 | 0 | 0 | 1 | 0 | 1 | 1 | 0 | 1 | 1
0 | 1 | 0 | 0 | 0 | 0 | 1 | 1 | 1 | 1
0 | 0 | 0 | 0 | 0 | 1 | 1 | 1 | 1 | 1
0 | 0 | 1 | 1 | 0 | 1 | 0 | 0 | 1 | 1
0 | 0 | 0 | 0 | 0 | 1 | 1 | 1 | 1 | 1
0 | 0 | 0 | 0 | 0 | 1 | 1 | 1 | 1 | 1
Concat | Hex | Decimal | Concat opposite for
| | | Arduino | New
| | | | hex | New
| | | | | dec
00001101 | D | 13 | 10110000 | B0 | 176
11110010 | F2 | 242 | 01001111 | 4F | 79
01111000 | 78 | 120 | 00011110 | 1E | 30
00011110 | 1E | 30 | 01111000 | 78 | 120
00101101 | 2D | 45 | 10110100 | B4 | 180
10000111 | 87 | 135 | 11100001 | E1 | 225
00001111 | F | 15 | 11110000 | F0 | 240
01101001 | 69 | 105 | 10010110 | 96 | 150
00001111 | F | 15 | 11110000 | F0 | 240
00001111 | F | 15 | 11110000 | F0 | 240

Table 12: Table for the signals, their converted decimal and hexadecimal equivalents, and the desired Arduino code for Induction Heater On State

State: Induction heater intermediate on Start
bit | Data bits (one byte) | End
bit
0 | 0 | 0 | 0 | 0 | 1 | 1 | 0 | 1 | 1
0 | 1 | 1 | 1 | 1 | 0 | 0 | 1 | 0 | 1
0 | 0 | 1 | 0 | 1 | 1 | 0 | 1 | 0 | 1
0 | 0 | 0 | 0 | 1 | 1 | 1 | 1 | 0 | 1
0 | 0 | 0 | 1 | 0 | 1 | 1 | 0 | 1 | 1
0 | 1 | 0 | 0 | 0 | 0 | 1 | 1 | 1 | 1
0 | 0 | 0 | 0 | 0 | 1 | 1 | 1 | 1 | 1
0 | 0 | 1 | 1 | 0 | 1 | 0 | 0 | 1 | 1
0 | 0 | 0 | 0 | 0 | 1 | 1 | 1 | 1 | 1
0 | 0 | 0 | 0 | 0 | 1 | 1 | 1 | 1 | 1
Concat | Hex | Decimal | Concat opposite for
| | | Arduino | New
| | | | hex | New
| | | | | dec
00001101 | D | 13 | 10110000 | B0 | 176
11110010 | F2 | 242 | 01001111 | 4F | 79
01011010 | 5A | 90 | 01011010 | 5A | 90
00011110 | 1E | 30 | 01111000 | 78 | 120
00101101 | 2D | 45 | 10110100 | B4 | 180
10000111 | 87 | 135 | 11100001 | E1 | 225
00001111 | F | 15 | 11110000 | F0 | 240
01101001 | 69 | 105 | 10010110 | 96 | 150
00001111 | F | 15 | 11110000 | F0 | 240
00001111 | F | 15 | 11110000 | F0 | 240

Table 13: Table for the signals, their converted decimal and hexadecimal equivalents, and the desired Arduino code for Induction Heater Intermediate On State

State: Induction heater off Start
bit | Data bits (one byte) | End
bit
0 | 0 | 0 | 0 | 0 | 1 | 1 | 0 | 1 | 1
0 | 1 | 1 | 1 | 1 | 0 | 0 | 1 | 0 | 1
0 | 0 | 0 | 0 | 0 | 1 | 1 | 1 | 1 | 1
0 | 0 | 0 | 1 | 1 | 1 | 1 | 0 | 0 | 1
0 | 0 | 0 | 1 | 0 | 1 | 1 | 0 | 1 | 1
0 | 1 | 0 | 0 | 0 | 0 | 1 | 1 | 1 | 1
0 | 0 | 0 | 0 | 0 | 1 | 1 | 1 | 1 | 1
0 | 0 | 1 | 1 | 0 | 1 | 0 | 0 | 1 | 1
0 | 0 | 0 | 0 | 0 | 1 | 1 | 1 | 1 | 1
0 | 0 | 0 | 0 | 0 | 1 | 1 | 1 | 1 | 1

Concat | Hex | Decimal | Concat opposite for
| | | Arduino | New
| | | | hex | New
| | | | | dec
00001101 | D | 13 | 10110000 | B0 | 176
11110010 | F2 | 242 | 01001111 | 4F | 79
00001111 | F | 15 | 11110000 | F0 | 240
00111100 | 3C | 60 | 00111100 | 3C | 60
00101101 | 2D | 45 | 10110100 | B4 | 180
10000111 | 87 | 135 | 11100001 | E1 | 225
00001111 | F | 15 | 11110000 | F0 | 240
01101001 | 69 | 105 | 10010110 | 96 | 150
00001111 | F | 15 | 11110000 | F0 | 240
00001111 | F | 15 | 11110000 | F0 | 240

Table 14: Table for the signals, their converted decimal and hexadecimal equivalents, and the desired Arduino code for Induction Heater Off State

## E Data Sheets

The data sheets for components used in this project are attached in the following order: water pump, temperature sensor, NPN MOSFET, JQX relay switch, IOT relay switch, Op Amp, and servo.

# KPM27D(U)

### Air Pressure Pump

# Specifications

## Applications

## Blood Pressure M/C, Health Care, Bidet Massager, Medical Equipment, etc

1. Rated Voltage . Rated Voltage | DC6.0V (D-type) | DC6.0V (U-type)
2. Rated Current . Rated Current | <430mA | <410mA
3. Inflation Time . Inflation Time | <10 S (From 0 to 300 mmHg in a 500CC tank.)
4. Air Flow Without Load . Air Flow Without Load | >2.0LPM
5. Max Pressure Max. Pressure | >350mmHg 350mmHg
6. Leakage . Leakage | Max. 3 mmHg/min from 300mmHg at 500CC tank.
7. Noise Level . Noise Level | 65dB (30cm away) | 55dB (30cm away)
8. Apply For . Apply For | Air

# Drawing

## www.yujinelectric.com

## General Description

The DS18B20 digital thermometer provides 9-bit to 12-bit Celsius temperature measurements and has an alarm function with nonvolatile user-programmable upper and lower trigger points. The DS18B20 communicates over a 1-Wire bus that by definition requires only one data line (and ground) for communication with a central microprocessor. In addition, the DS18B20 can derive power directly from the data line (“parasite power”), eliminating the need for an external power supply.
Each DS18B20 has a unique 64-bit serial code, which allows multiple DS18B20s to function on the same 1-Wire bus. Thus, it is simple to use one microprocessor to control many DS18B20s distributed over a large area. Applications that can benefit from this feature include HVAC environmental controls, temperature monitoring systems inside buildings, equipment, or machinery, and process monitoring and control systems.

## Applications

- Thermostatic Controls
- Industrial Systems
- Consumer Products
- Thermometers
- Thermally Sensitive Systems

## Benefits and Features

- Unique 1-Wire® Interface Requires Only One Port Pin for Communication
- Reduce Component Count with Integrated Temperature Sensor and EEPROM
- Measures Temperatures from -55°C to +125°C (-67°F to +257°F)
- ±0.5°C Accuracy from -10°C to +85°C
- Programmable Resolution from 9 Bits to 12 Bits
- No External Components Required
- Parasitic Power Mode Requires Only 2 Pins for Operation (DQ and GND)
- Simplifies Distributed Temperature-Sensing Applications with Multidrop Capability
- Each Device Has a Unique 64-Bit Serial Code Stored in On-Board ROM
- Flexible User-Definable Nonvolatile (NV) Alarm Settings with Alarm Search Command Identifies Devices with Temperatures Outside Programmed Limits
- Available in 8-Pin SO (150 mils), 8-Pin µSOP, and 3-Pin TO-92 Packages

19-7487; Rev 6; 7/19

Ordering Information appears at end of data sheet.

1-Wire is a registered trademark of Maxim Integrated Products, Inc.
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

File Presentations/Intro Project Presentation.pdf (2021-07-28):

# The Perfect Chai Maker

# Awnit Singh Marta

# Perfect Chai

# Perfect Chai

Making coffee at the workplace has become an integrated part of workflow, generally requiring just the touch of a button to make. However, making Chai, a South Asian tea, or the closest alternative, has required more time, preparation, and handling of multiple components.

# Chai

### - Indian Tea

### - English Breakfast

- + spices, loose leaf

### - Stovetop

### - Boiled water… boiled milk


# Chai

### - Indian Tea

### - Exotic English Breakfast

- + spices, loose leaf

### - Stovetop

### - Boiled water… boiled milk

Temperatures to be determined “experimentally”


# Perfect Chai Maker?

Making coffee at the workplace has become an integrated part of workflow, generally requiring just the touch of a button to make. However, making Chai, a South Asian tea, or the closest alternative, has required more time, preparation, and handling of multiple components.

# Perfect Chai Maker?

Making coffee at the workplace has become an integrated part of workflow, generally requiring just the touch of a button to make. However, making Chai, a South Asian tea, or the closest alternative, has required more time, preparation, and handling of multiple components.

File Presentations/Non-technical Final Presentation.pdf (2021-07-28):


# The Perfect Chai Maker

A recipe by
Awnit Singh Marta
Advisor: Dr Nathan Taylor
Reader: Prof David Brooks

# Problem

Institute for Scientific Information on Coffee, “The good things in life: coffee in the workplace,” Worcestershire, 2017.

Chai: a flavour NOT a process No dedicated chai machine in market

2 billion tea drinkers ↑+ in American market (Starbucks, Peet’s, 7/11)


67% drink ‘hot beverages’ at workplace: taste, socialize, pause & rest
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

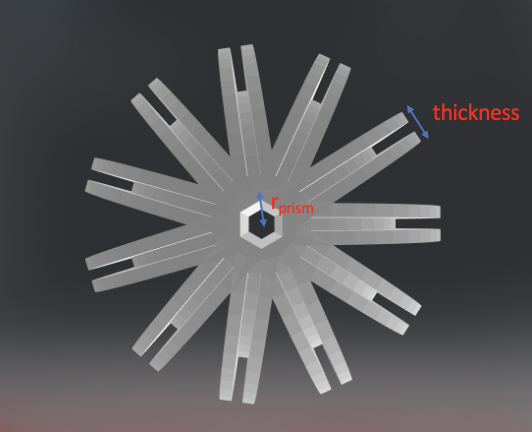
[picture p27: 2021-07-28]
Pictures/rottop.png

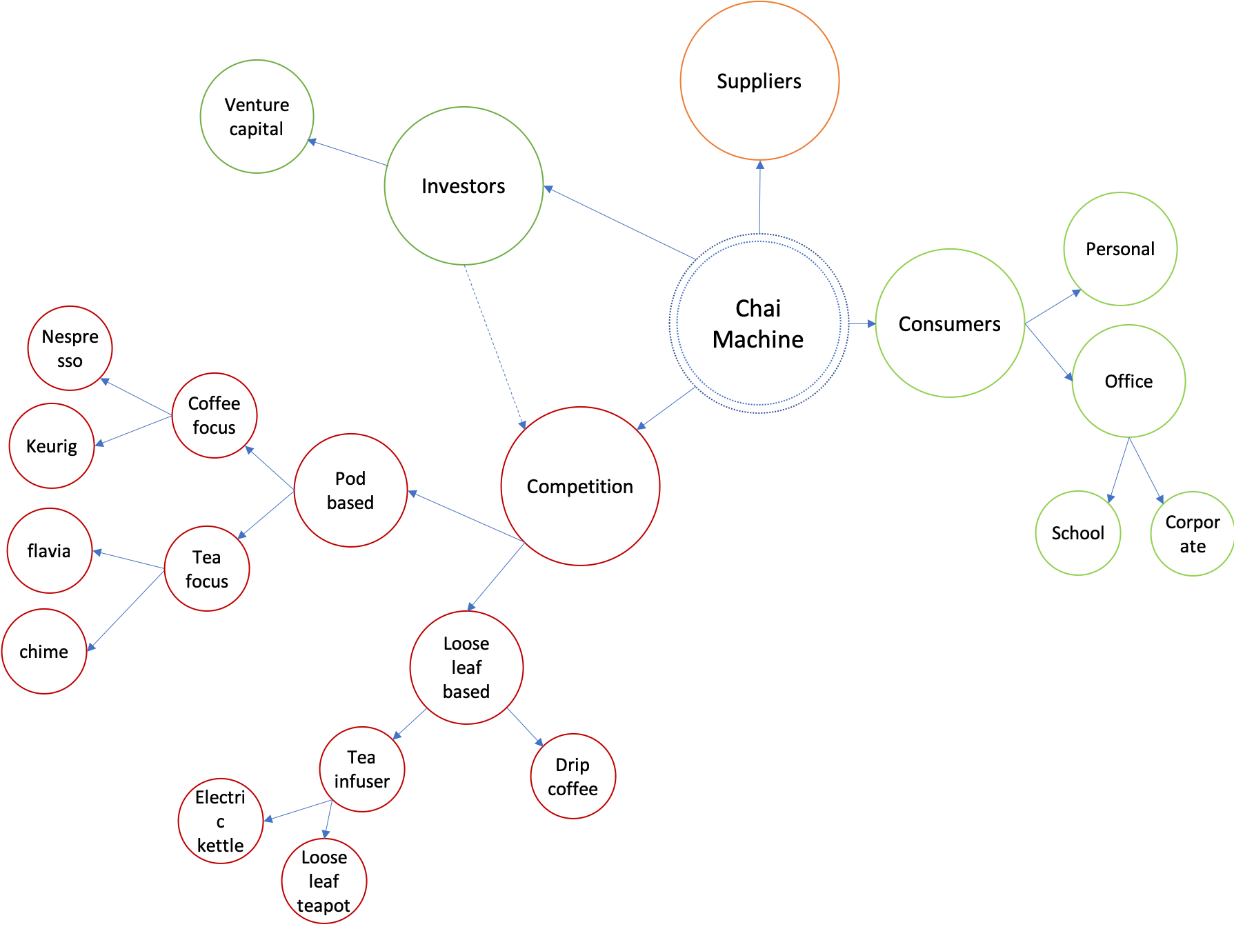
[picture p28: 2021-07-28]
Figures/stakeholdermap.png

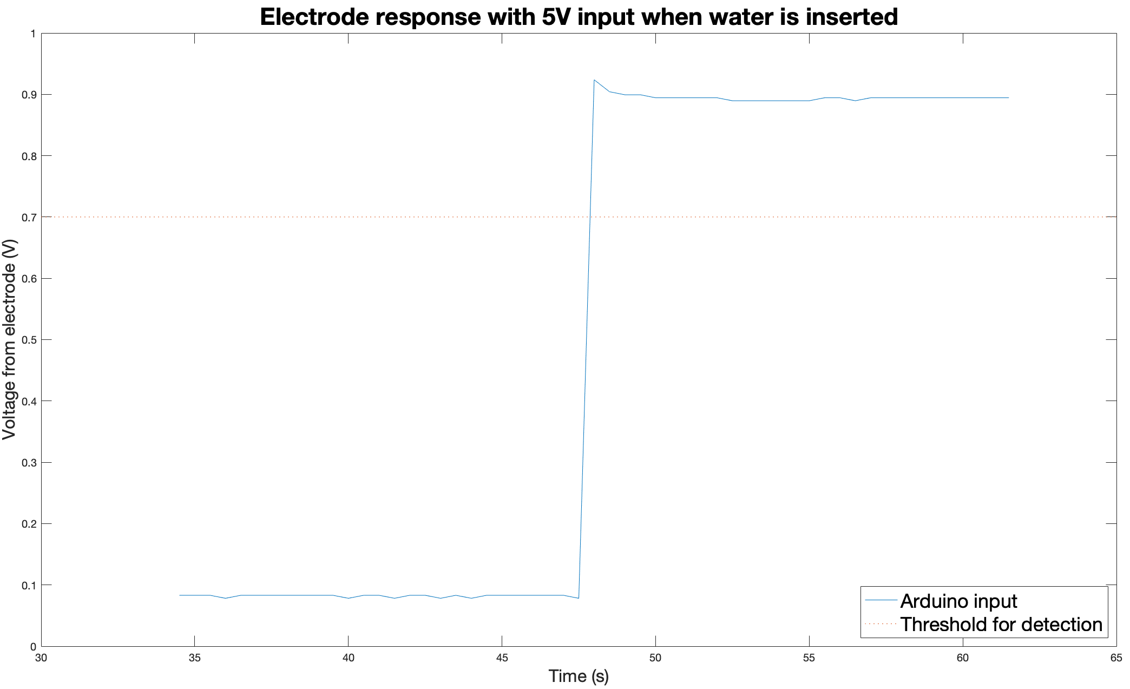
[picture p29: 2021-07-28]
Figures/electroderesponse2.png

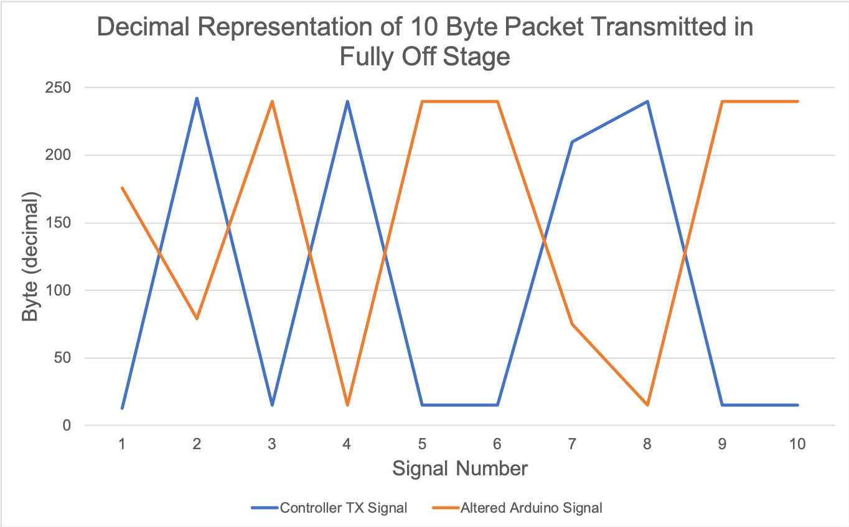
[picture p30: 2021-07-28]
Figures/induction-code.png

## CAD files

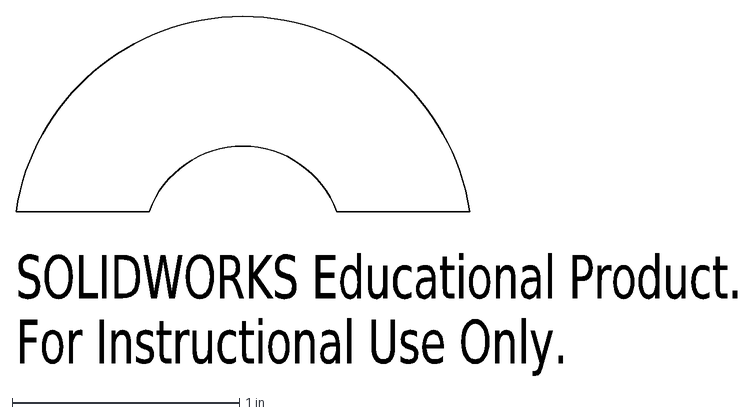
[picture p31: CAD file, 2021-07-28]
CAD/asm-silicone-inserts17.5mm.DXF
SOLIDWORKS Educational Product.
For Instructional Use Only.

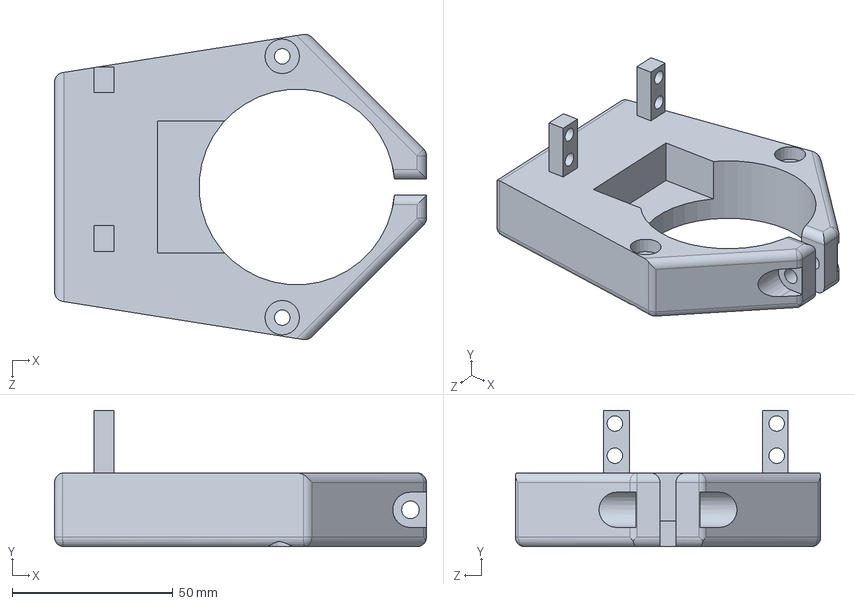
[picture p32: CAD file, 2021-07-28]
CAD/Builders/asm-clamp.SLDPRT
115.8 x 42.5 x 95.1 mm

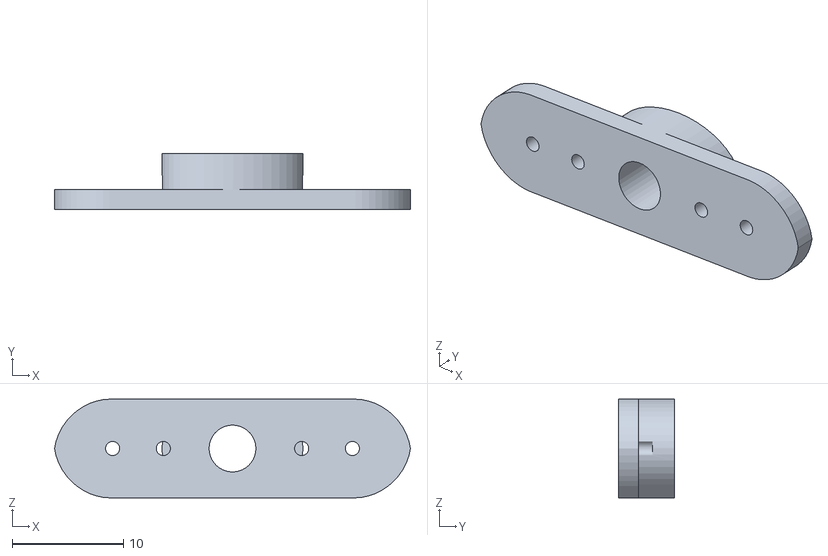
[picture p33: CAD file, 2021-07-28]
CAD/asm-servoattachmentv2STL.STL
32.1 x 5.00 x 8.89

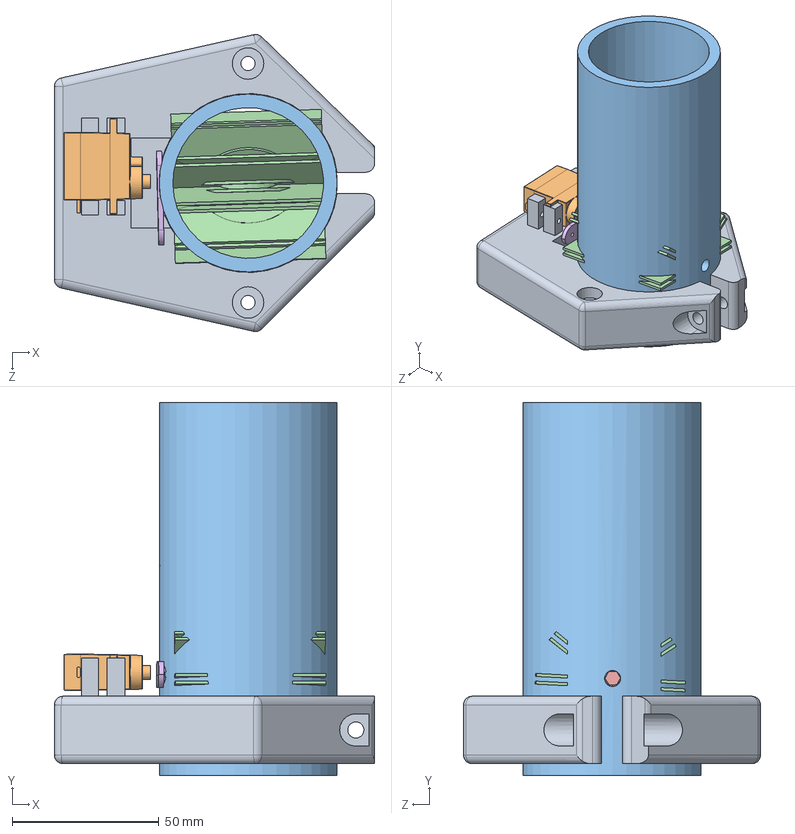
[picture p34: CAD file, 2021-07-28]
CAD/Builders/Assem1.SLDASM
109.1 x 127.0 x 101.2 mm
asm-clamp
TowerPro SG92R Servo Motor
PVC-PIPE
asm-sugar-17.5mm
asm-hexrod
asm-servoattachment

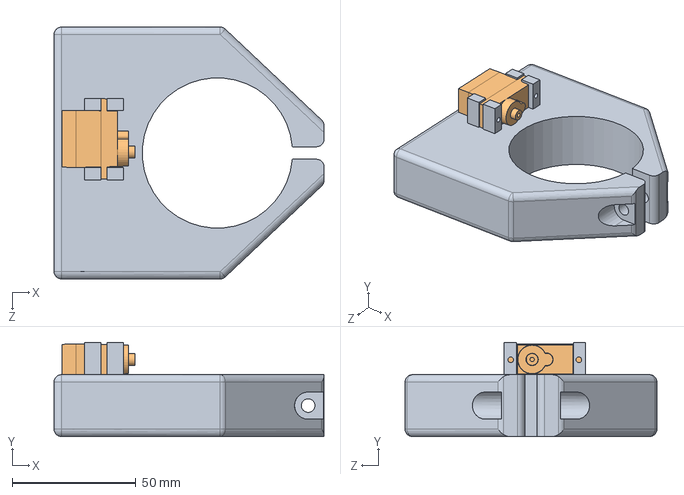
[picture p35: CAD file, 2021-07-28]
CAD/Assem1.SLDASM
109.1 x 38.0 x 101.7 mm
asm-clamp
TowerPro SG92R Servo Motor

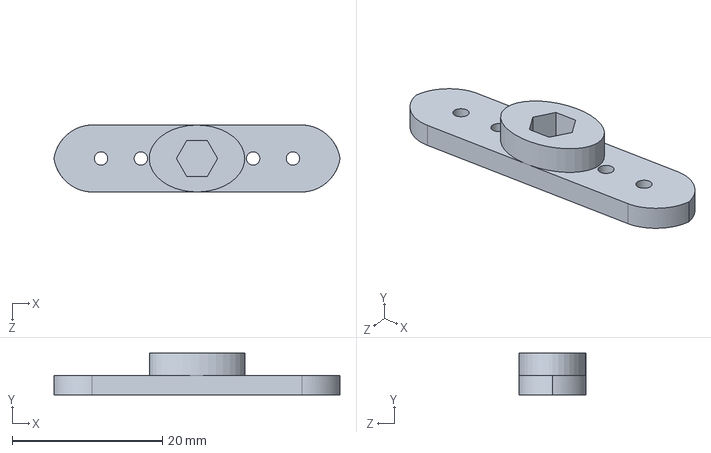
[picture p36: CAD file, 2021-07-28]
CAD/Builders/asm-servoattachment.SLDPRT
38.0 x 5.54 x 8.89 mm

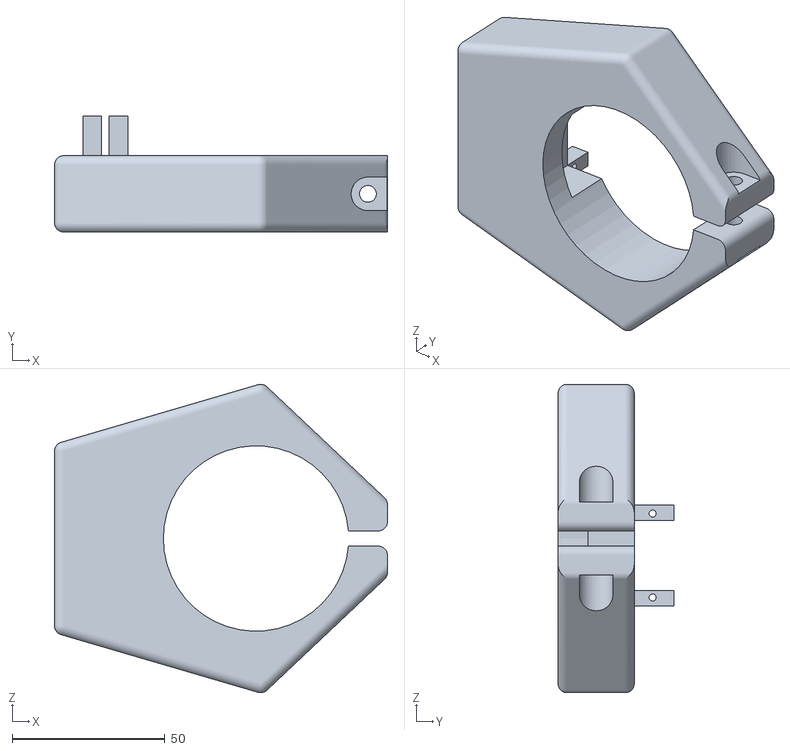
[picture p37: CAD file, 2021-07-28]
CAD/asm-clampv2.STL
109.1 x 38.0 x 101.0

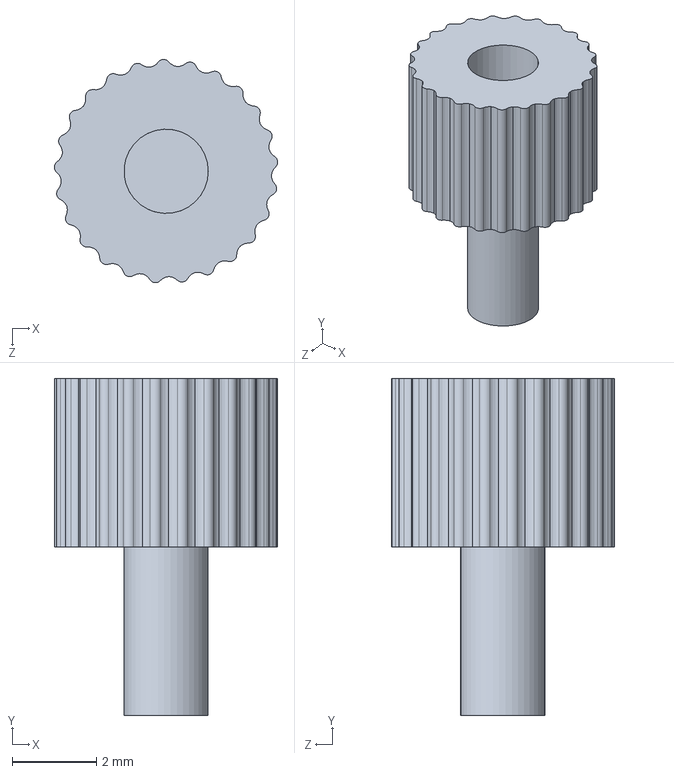
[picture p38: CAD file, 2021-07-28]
CAD/Servomoteur SM-S4303R.SLDASM
5.30 x 8.00 x 5.30 mm

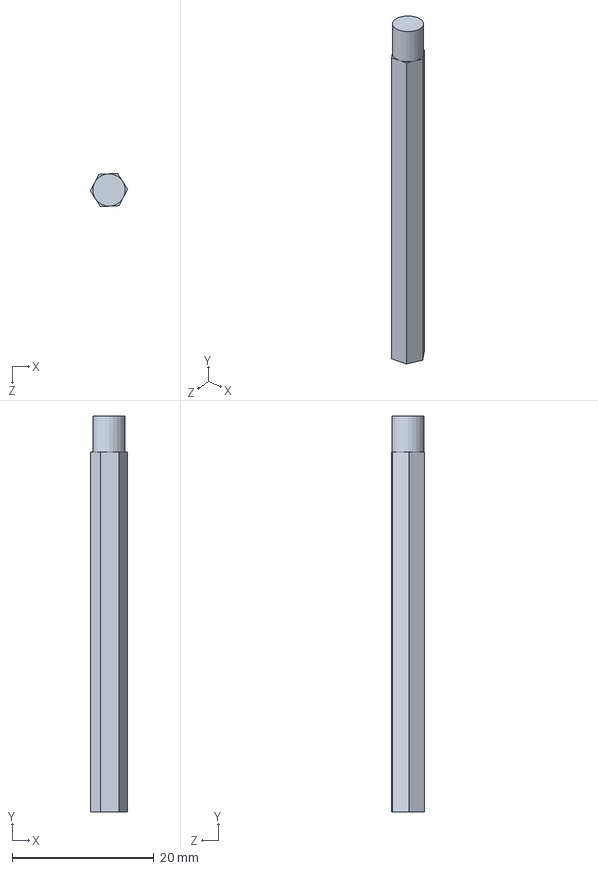
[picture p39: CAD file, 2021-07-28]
CAD/asm-hexrod.SLDPRT
5.27 x 55.9 x 4.71 mm

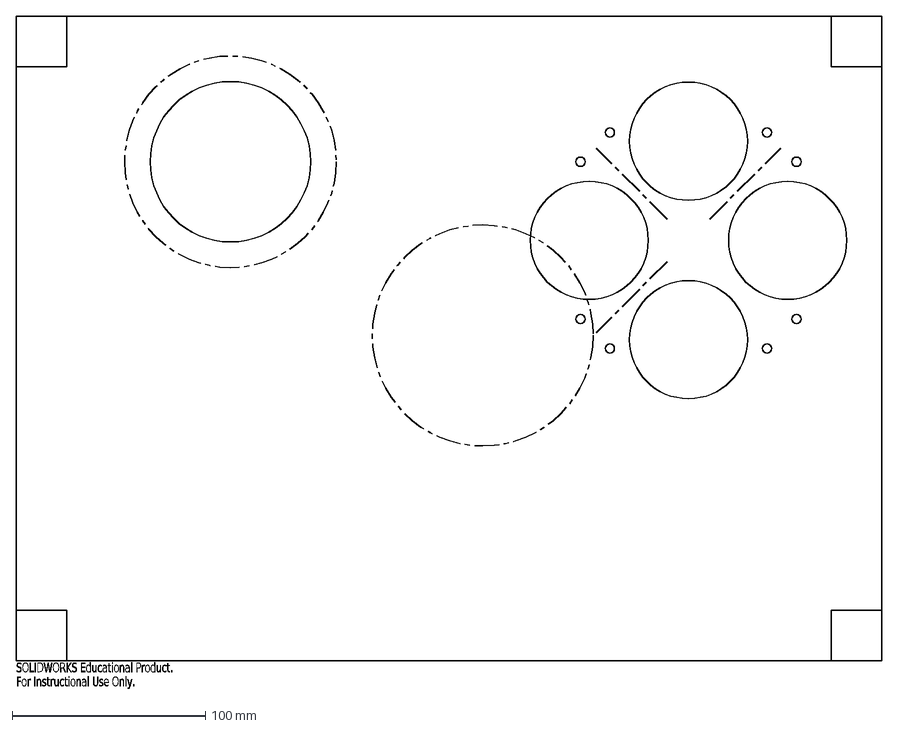
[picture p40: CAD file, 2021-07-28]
CAD/board.DXF
SOLIDWORKS Educational Product.
For Instructional Use Only.

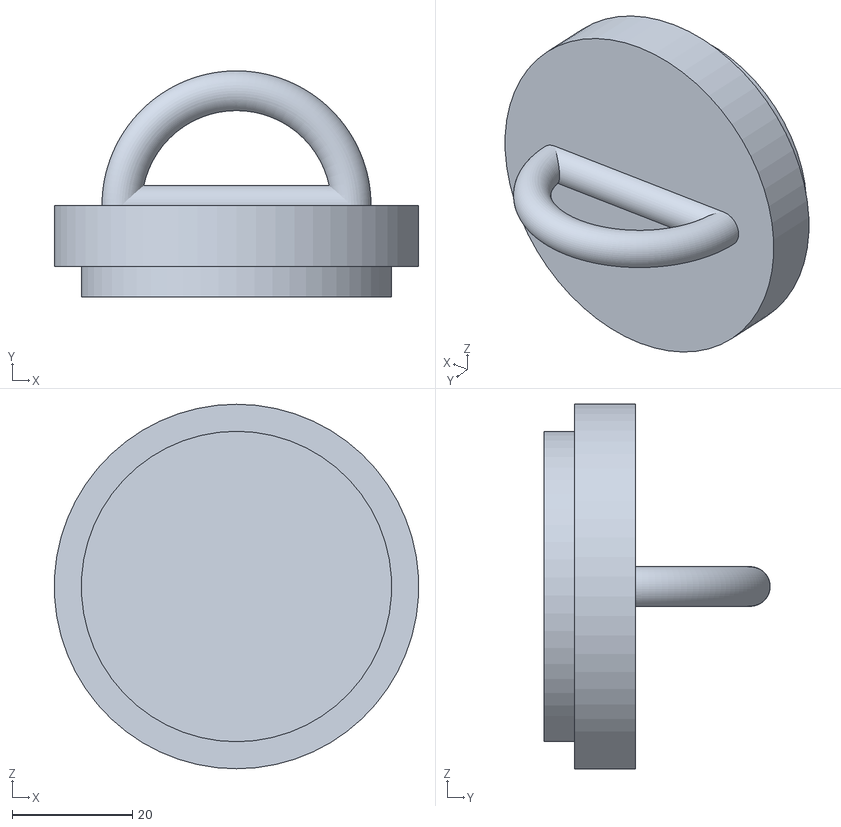
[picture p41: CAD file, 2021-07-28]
CAD/lid.STL
60.5 x 37.6 x 60.6

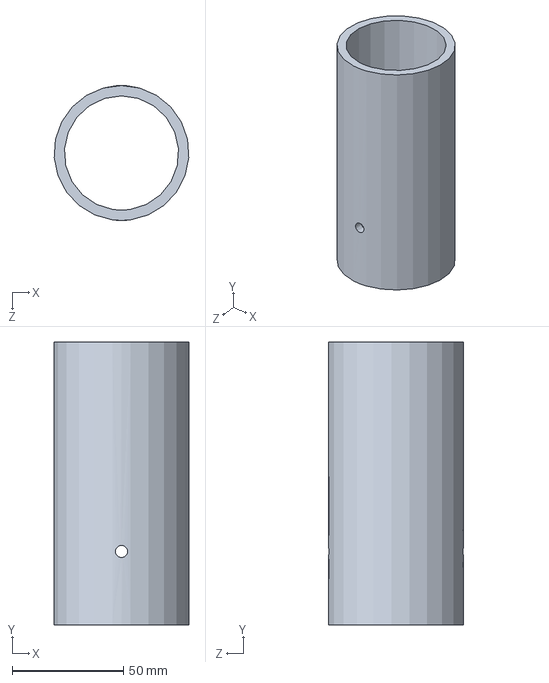
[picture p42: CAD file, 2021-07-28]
CAD/PVC-PIPE.SLDPRT
60.4 x 127.0 x 60.5 mm

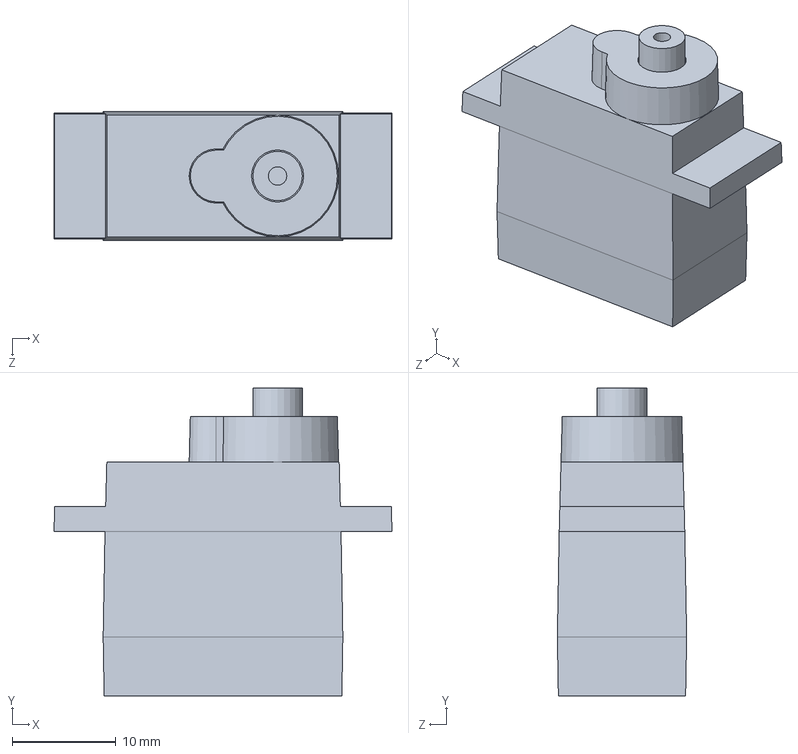
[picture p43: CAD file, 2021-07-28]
CAD/TowerPro SG92R Servo Motor.SLDPRT
32.5 x 29.6 x 12.4 mm

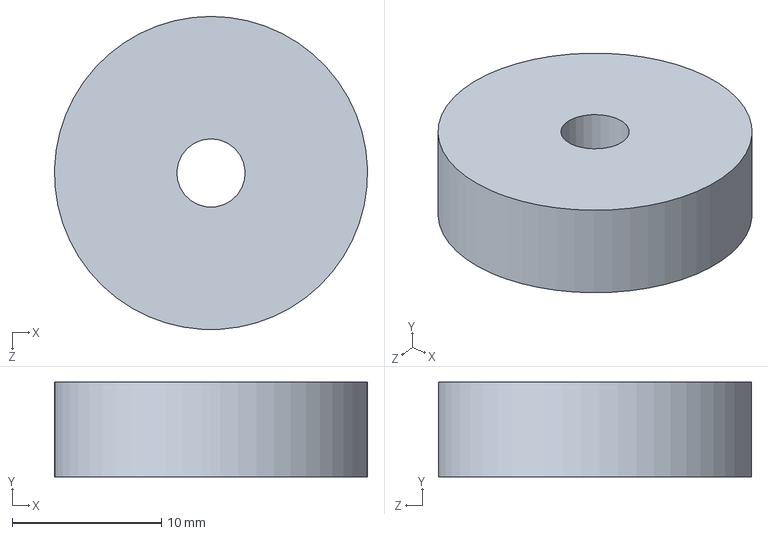
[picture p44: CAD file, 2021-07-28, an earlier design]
CAD/old/asm-attacher.SLDPRT
20.9 x 6.35 x 21.0 mm

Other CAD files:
CAD/Builders/asm-silicone-inserts.SLDPRT
CAD/asm-servoattachment.SLDPRT
CAD/asm-silicone-inserts.SLDPRT
CAD/Embout.SLDPRT
CAD/Builders/asm-servoattachment.STL
CAD/Builders/asm-silicone-inserts.DXF
CAD/Embout.STL
CAD/asm-hexrod.STL
CAD/asm-silicone-inserts.DXF
CAD/old/asm-attacher.STL
CAD/old/asm-clamp.STL
CAD/old/asm-servoattachmentSTL.STL
